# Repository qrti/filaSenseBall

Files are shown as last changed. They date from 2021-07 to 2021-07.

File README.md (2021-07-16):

# **Filament Runout Sensor with Steel Ball**

### Reliable and simple filament runout detection with low friction

<br>

## Operation
A steel ball is caught above the filament and drops into a light barrier if filament runs out. To reload filament a magnet is used to lift the steel ball. A cap allows closing and opening the housing.

### LED
Filament state is indicated by LED
- **on**  
loaded
- **off**  
runout

### Assembly
The three housing parts are printed flat sides down with support enabled at about 20 % fill rate. After printing the housing halves are glued together with hard plastic glue or superglue and the seams welded with a soldering iron (at about 200 °C for PLA). The fork light barrier is cut in half and plugged into the housing bottom. A suitable piece of perforated or drilled PCB is soldered to the light barrier leads. The PCB can be screwed to the little holes on the housing bottom. The little holes may need careful re-drilling according to the used screws. Electronic components, LED and printer connector are now soldered on the PCB. An 8 mm steel ball is put into the housing, the printed cap snap-closes it. 

### Files
[-> 3d print](stl)   
q5 prefix files are tailored for Flsun delta printer Q5

[-> schematic](#schematic)

### Thingiverse
https://www.thingiverse.com/thing:4902782

<br>

---

<br>

## Views

Mounted sensor   
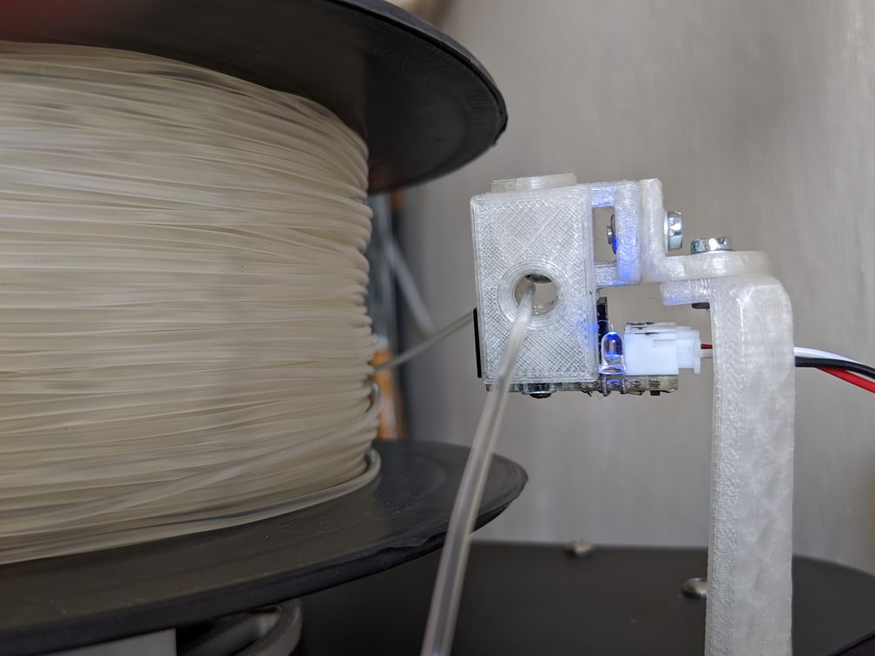
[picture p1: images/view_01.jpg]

<br>
<br>

To adapt to filament tension the sensor can be tilted   
if smoothly printed a tilt angel up to 85 degree should be possible   
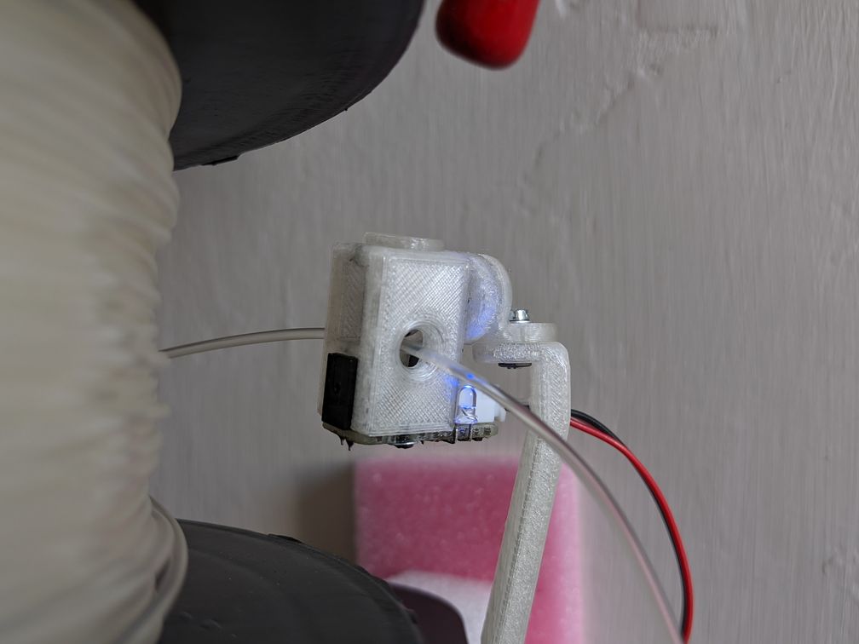
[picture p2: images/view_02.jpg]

<br>
<br>

A mounting bracket allows adjusting tilt and top angle   
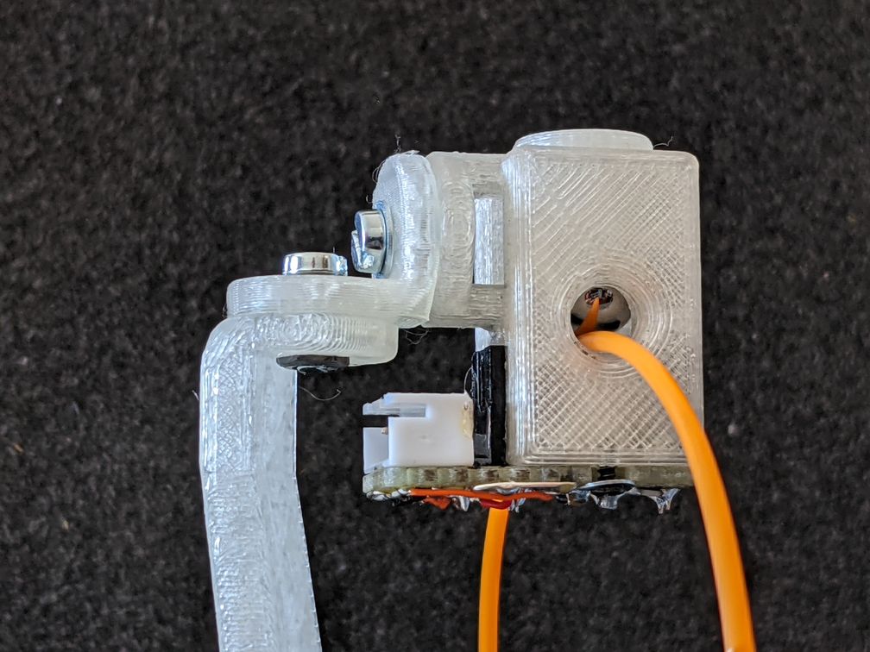
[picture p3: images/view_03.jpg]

<br>
<br>

## Renders

Steel ball above filament   
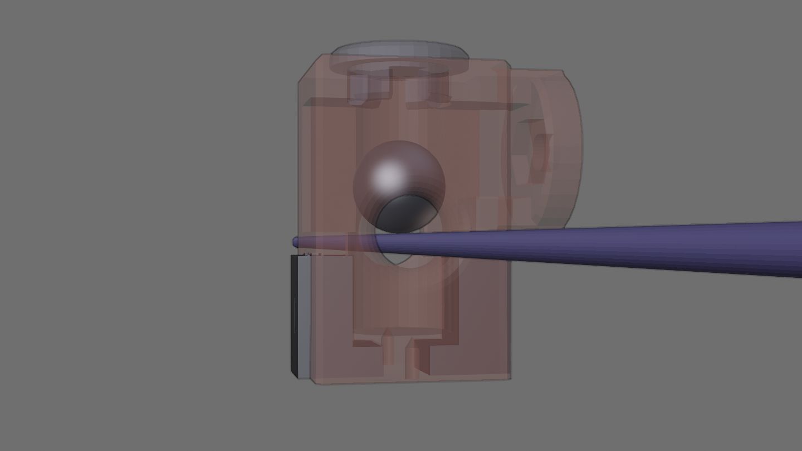
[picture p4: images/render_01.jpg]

<br>
<br>

Steel ball dropped into light barrier   
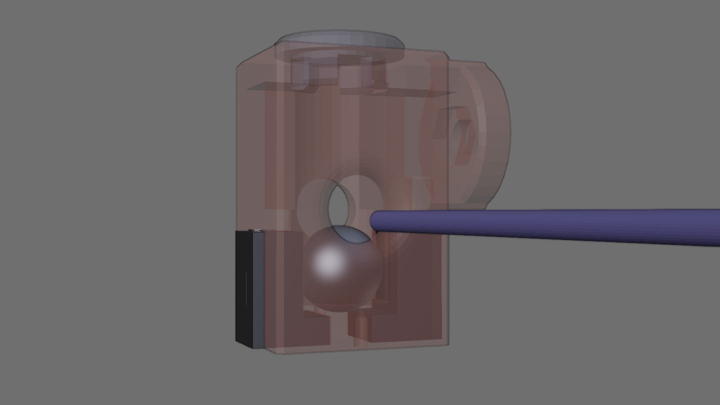
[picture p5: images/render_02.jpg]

<br>
<br>

Bottom with light barrier halves   
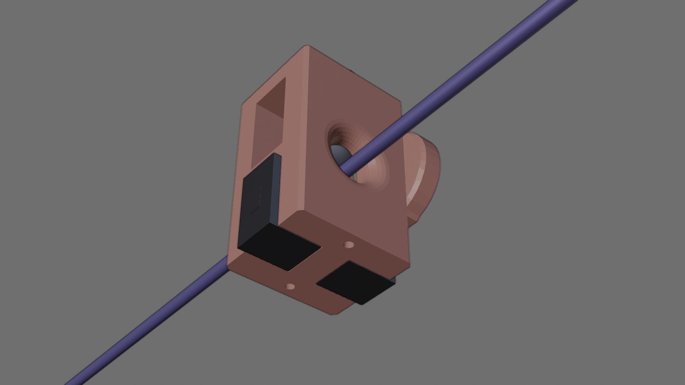
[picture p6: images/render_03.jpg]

<br>
<br>

Front   
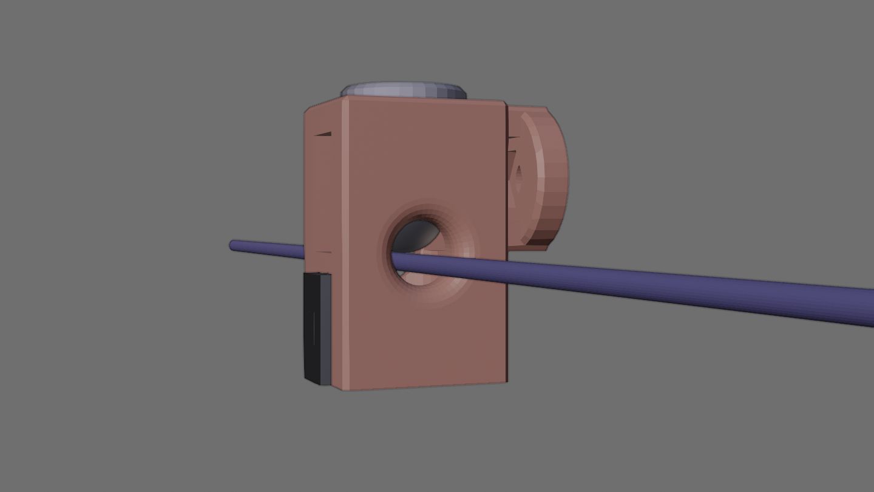
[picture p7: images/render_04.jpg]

<br>
<br>

Side   
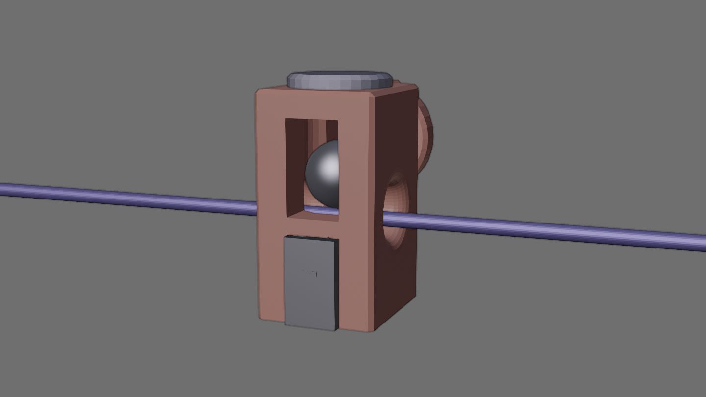
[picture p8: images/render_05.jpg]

<br>
<br>

## Schematic
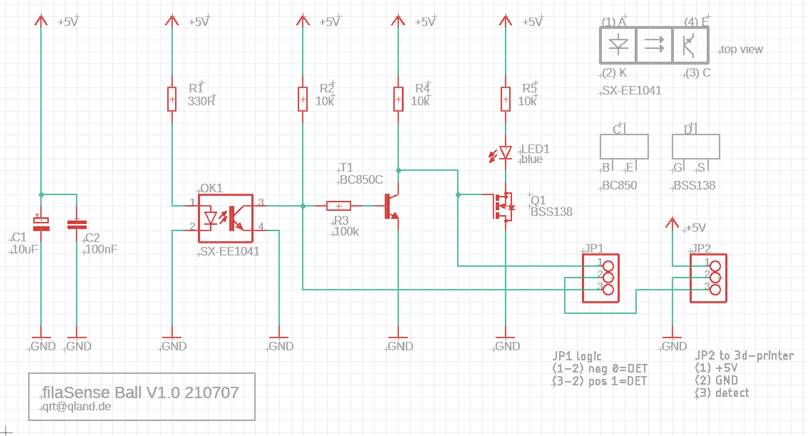
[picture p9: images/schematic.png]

<br>
<br>

<br>
<br>

---

[qrt@qland.de](mailto:qrt@qland.de) 210716

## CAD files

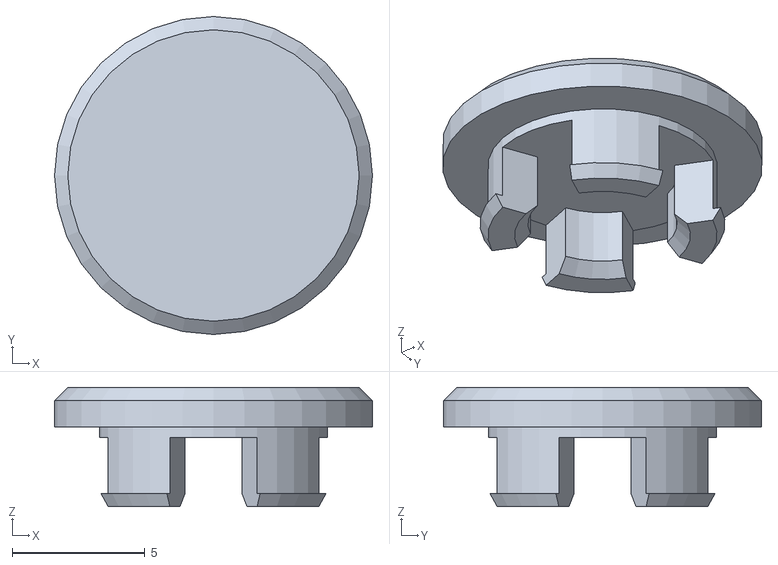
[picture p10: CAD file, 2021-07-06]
stl/housing_cap.stl
12.0 x 12.0 x 4.50

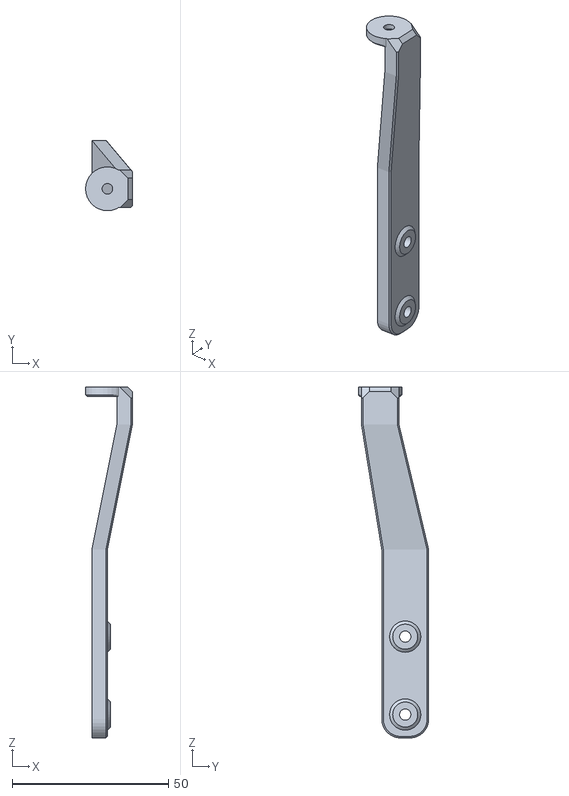
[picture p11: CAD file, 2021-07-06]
stl/q5_arm.stl
15.0 x 22.5 x 112.2

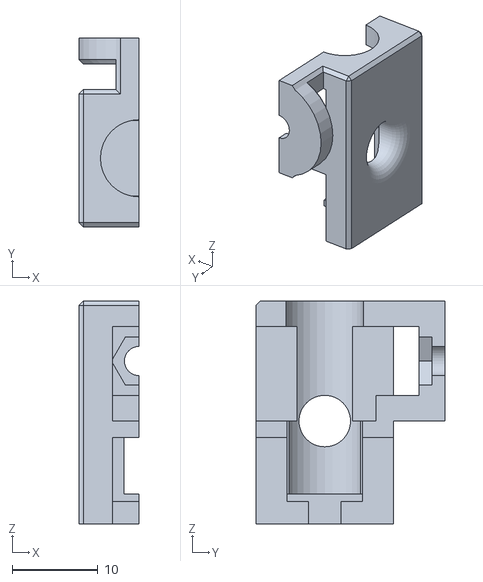
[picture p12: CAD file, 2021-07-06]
stl/housing_left.stl
7.00 x 22.0 x 26.0

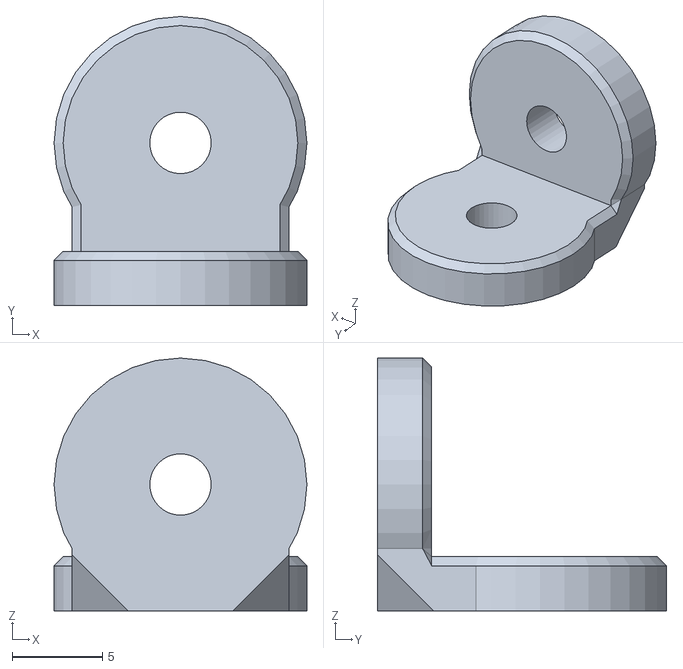
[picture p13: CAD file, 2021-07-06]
stl/q5_arm_link.stl
14.0 x 16.0 x 14.0

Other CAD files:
stl/housing_right.stl
